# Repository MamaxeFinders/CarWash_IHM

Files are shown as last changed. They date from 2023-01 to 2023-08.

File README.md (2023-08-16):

## The whole operation is devided into the following module.

 * [**HARDWARE SETUP**](#hardware-setup)
    * [**SYSTEM MODULE**](#system-module)
    * [**CAISSE MODULE**](#caisse-module)

 * [**SOFTWARE SETUP**](#software-setup)
    * [**SYSTEM MODULE**](#module-system)
    * [**CAISSE MODULE**](#module-caisse)
    
 * [**INITIALISATION**](#initialisation)
    * [**SYSTEM INITIALISATION**](#system-initialisation)
    * [**CAISSE INITIALISATION**](#caisse-initialisation)
 
# HARDWARE SETUP

## SYSTEM MODULE

The system module utilizes the following components:
1.  [ESP32 board](https://www.espressif.com/en/products/socs/esp32)
2.  [MAX6675 thermocouple module](https://www.analog.com/media/en/technical-documentation/data-sheets/MAX6675.pdf)
3.  Four 5V LEDs is connected with the ESP32. The number of LEDs may vary depending on the number of CAISSE module.

**ESP32 board** pinout diagram:
ESP32 pinout


**MAX6675** thermocouple module pinout:
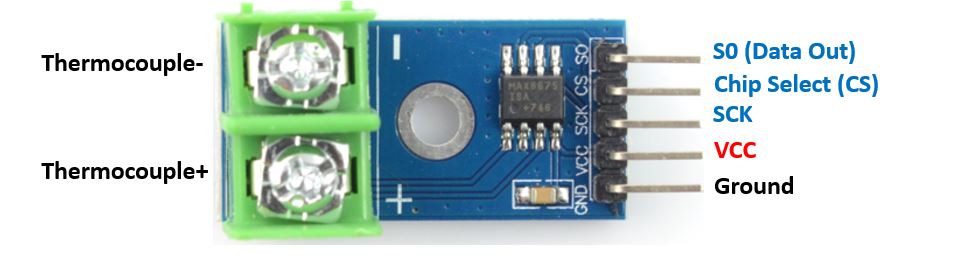
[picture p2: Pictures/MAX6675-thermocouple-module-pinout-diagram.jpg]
MAX6675 thermocouple module


The MAX6675 thermocouple is connecteded to the ESP32 as follorwing:
1.  S0 pin to GPIO27
2.  CS pin to GPIO14
3.  SCK pin to GPIO12

The four LEDs indicating CAISSE module with be connected with GPIO 19, 18 ,5, 17 of the ESP32

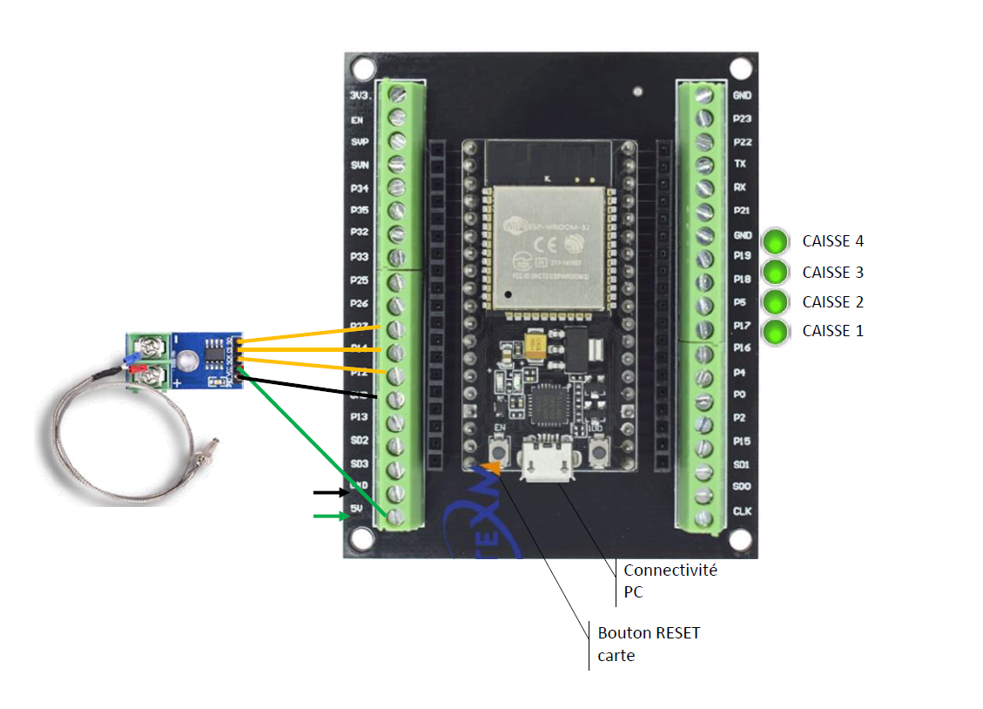
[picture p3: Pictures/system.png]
MAX6675 thermocoupleto ESP32


## CAISSE MODULE

The caisse module utilizes the following components: 
1.  [ESP32 board](https://www.espressif.com/en/products/socs/esp32)
2.  [SW-420 vibration-sensor-module](https://components101.com/sensors/sw-420-vibration-sensor-module)
3.  [2x16 LCD I2C display](https://components101.com/sites/default/files/components/16x2-LCD-Module.jpg)
4.  [8 channel 5V relay module](https://m.media-amazon.com/images/I/51BrNgOyHdL.jpg)
5.  A custom made PCB board (See GERBERS file)

**SW-420** vibration sensor module pinout diagram:
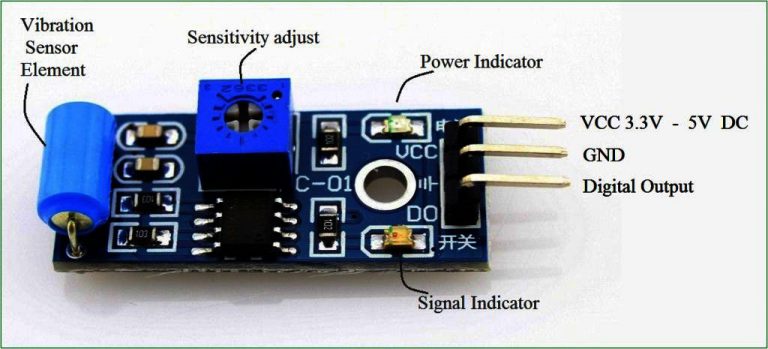
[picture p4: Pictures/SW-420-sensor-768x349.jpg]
SW-420 vibration-sensor-module pinout


**2x16 LCD I2C display** module pinout:
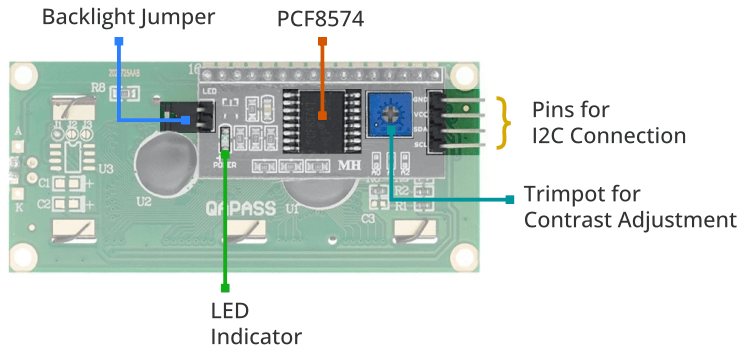
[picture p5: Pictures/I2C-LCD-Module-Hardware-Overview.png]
2x16 LCD I2C display pinout


**8 channel 5V relay** module pinout:
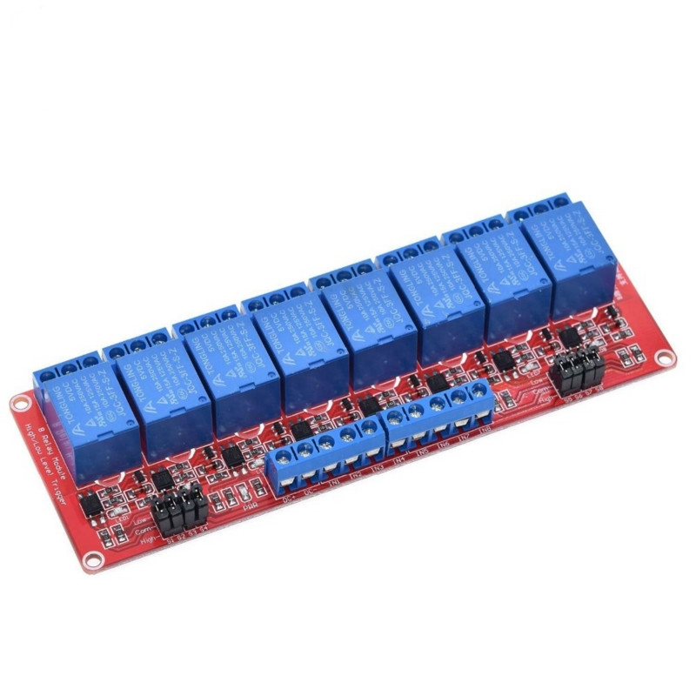
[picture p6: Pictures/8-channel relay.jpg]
8 channel 5V relay pinout


The SW-420 vibration-sensor-module is connecteded to the ESP32 as follorwing:
1.  D0 pin to GPIO13

The 2x16 LCD I2C display module is connecteded to the ESP32 as follorwing:
1.  SCL pin to GPIO22
2.  SDA pin to GPIO21

The 8 channel 5V relay module is connecteded to the ESP32 as follorwing:
1.  Relay 1 input pin to GPIO19
2.  Relay 2 input pin to GPIO18
3.  Relay 3 input pin to GPIO5
4.  Relay 4 input pin to GPIO17
5.  Relay 5 input pin to GPIO16
6.  Relay 6 input pin to GPIO4
7.  Relay 7 input pin to GPIO0
8.  Relay 8 input pin to GPIO15

### CAISSE module pcb wiring layout

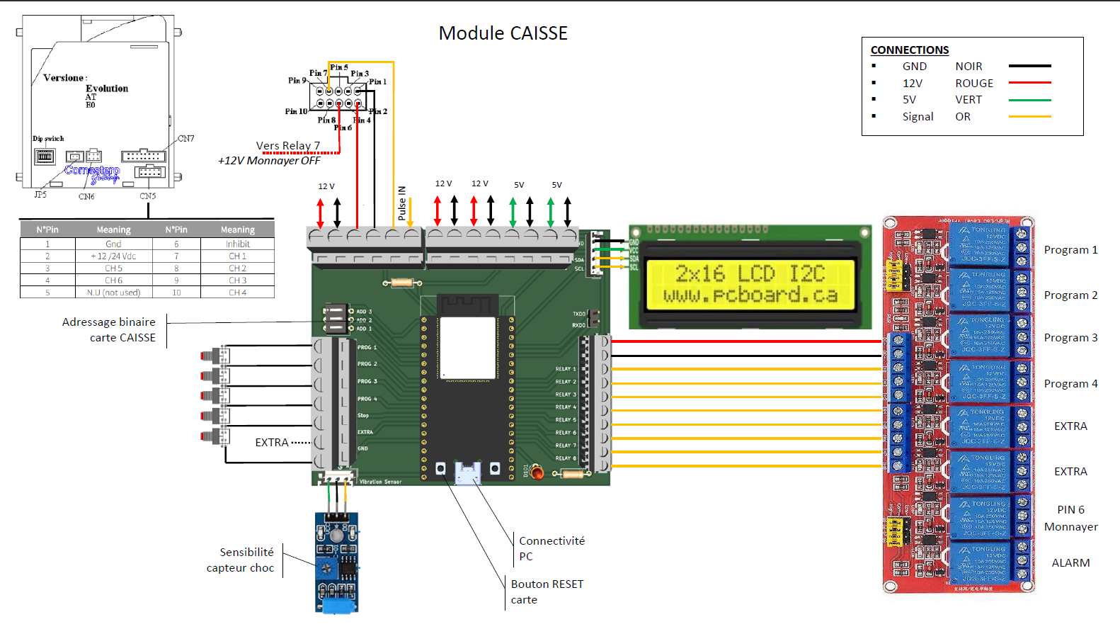
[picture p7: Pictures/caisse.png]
CAISSE module pcb wiring

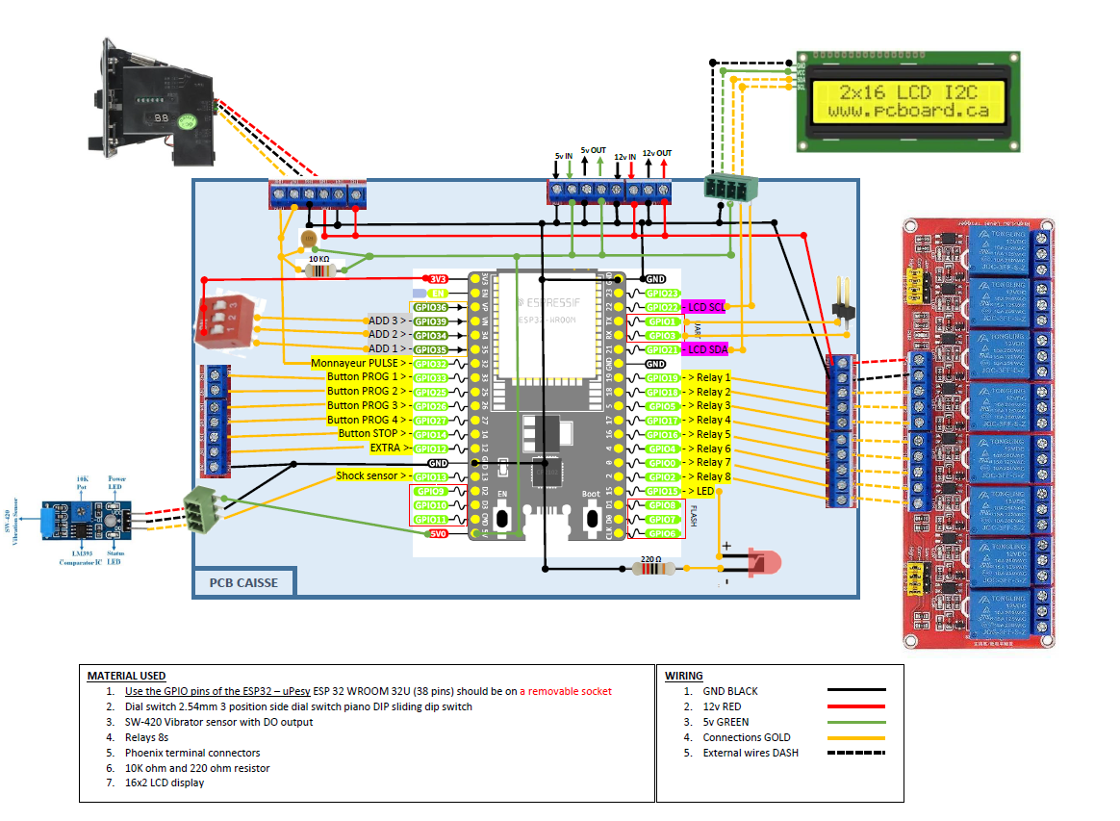
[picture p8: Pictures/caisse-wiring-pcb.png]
CAISSE module pcb schematics


### GERBER FILE
You can find the [caisse-module-gerber](https://github.com/MamaxeFinders/CarWash_IHM/tree/main/printed%20circuit%20boards) files here
 
# SOFTWARE SETUP

### ARDUINO IDE
Download and install the arduino ide by following this link [ARDUINO IDE](https://docs.arduino.cc/software/ide-v2/tutorials/getting-started/ide-v2-downloading-and-installing)

### ESP32 Add-on
Install ESP32 board add-on in Arduino IDE by following this link [ESP32 ADD-ON](https://randomnerdtutorials.com/installing-the-esp32-board-in-arduino-ide-windows-instructions/)

## Module SYSTEM

### WIFI manager library
The [*WiFiManager*](https://github.com/tzapu/WiFiManager) library for ESP32 provides an easy way to configure and manage WiFi connections in your projects. It offers features such as:
* Captive portal for setting WiFi credentials
* Ability to store WiFi credentials in Non-Volatile Memory (NVM)
* Option to automatically connect to a previously saved network
* Option to have multiple access points with custom settings
* Support for custom parameters in the configuration portal
To use the library, you can follow [this tutorial](https://microdigisoft.com/esp32-with-wifimanager-to-manage-ssid-and-password-no-hard-coding/) to setup and use the wifi-manager library. Then, you can initialize the WiFiManager object and use its functions to set up and control the WiFi connection.

### HTTPClient library
Install following this link [HTTPClient](https://github.com/amcewen/HttpClient)

### Thermocouple library
Install [MAX6675 library](https://github.com/adafruit/MAX6675-library) from the arduino library manager

### Universal Telegram Bot library
Install telegram bot library in Arduino IDE by following this link [UniversalTelegramBot](https://github.com/witnessmenow/Universal-Arduino-Telegram-Bot)

### Setup wifi as soft access point
Input your: ssid, password, channel, hide_SSID=true/false, max_connection

``` WiFi.softAP("SYSTEM_CAISSE", "123456789", CHANNEL, false, NUMSLAVES); ```

### Setup the google-script-id

``` String GOOGLE_SCRIPT_ID = "input your google-script-id here" ; ```

### Initialize Telegram BOT

``` String BOTtoken = "input your telegram bot-token here"; ```

### Compile and upload the code
Finally you can compile and upload the [system-module code](https://github.com/MamaxeFinders/CarWash_IHM/blob/main/codes/System_Auto_V3.ino) to your system module

## Module CAISSE

### LiquidCrystal_I2C library
Install [LiquidCrystal_I2C library](https://github.com/fdebrabander/Arduino-LiquidCrystal-I2C-library) from the arduino library manager

### Compile and upload the code
Finally you can compile and upload the [caisse-module code](https://github.com/MamaxeFinders/CarWash_IHM/blob/main/codes/Caisse_Auto_V3.ino) to your system module

# INITIALISATION

## SYSTEM INITIALISATION

* Turn on module SYSTEM by powering it to 5V DC. 
   * **Warning:** *Providing more than 5V will damage the module*
* Use your mobile device in order to connect to the ESP32 WiFi. Select SYSTEM_LAVAGE and connect using the password (123456789 by default).
* Wait for a windows to pop up. It will display the available networks found by the module. Click to the router you wish the module needs to connect to internet. Enter the password and click SAVE.
* Wait until the page disappear. If you go back to your WiFi settings you should now see an available SSID called SYSTEM_CAISSE which confirm the module is properly set *(DO NOT CONNECT TO THIS NEW NETWORK)*.

## CAISSE INITIALISATION

* Once the SYSTEM is connected, you can initiate the module CAISSE.
* As there can be multiple CAISSE, use the micro switch in order to address the module from 1 to 7 using the binary switches (we only used p to 4 CAISSEs here). 
* Then power it up and wait for the LED to turn on. If the module did not manage to connect to SYSTEM, the LED will blink 3 time before it restarts.
* An isolate mode is available if all switches are put to zero. The module CAISSE will start without connecting to the SYSTEM and can be used for test purpose.
* Once the module is connected and you can see the message *BONJOUR* on the LCD screen, turn OFF the module SYSTEM and ON again. Wait until the LED linked to the CAISSE id turns ON. This means both modules are ready to communicate as their mac addresses have been saved to both memories.
* Perform the same process as 2 for all other module CAISSE.

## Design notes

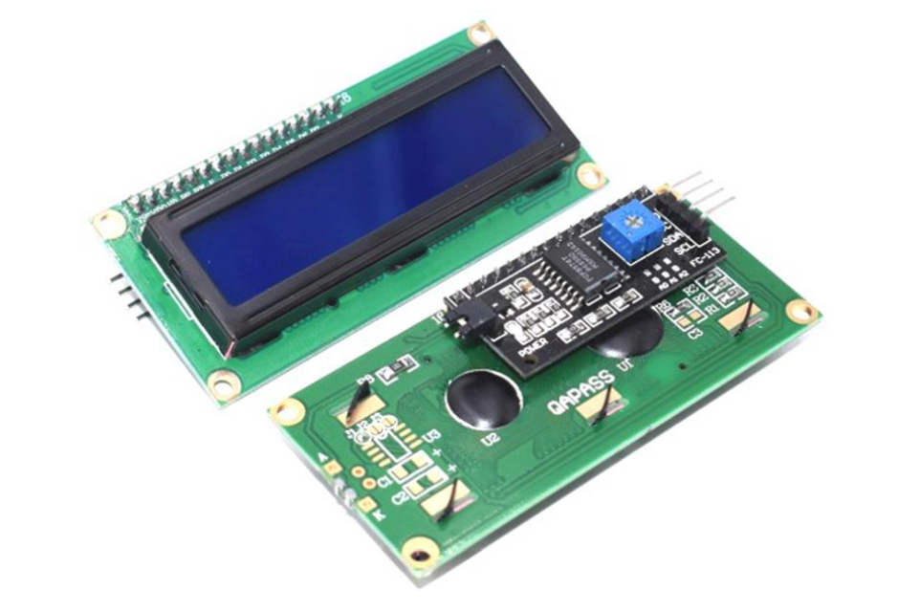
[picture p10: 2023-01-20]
Pictures/I2C-LCD-Module-Hardware-Overview2.png

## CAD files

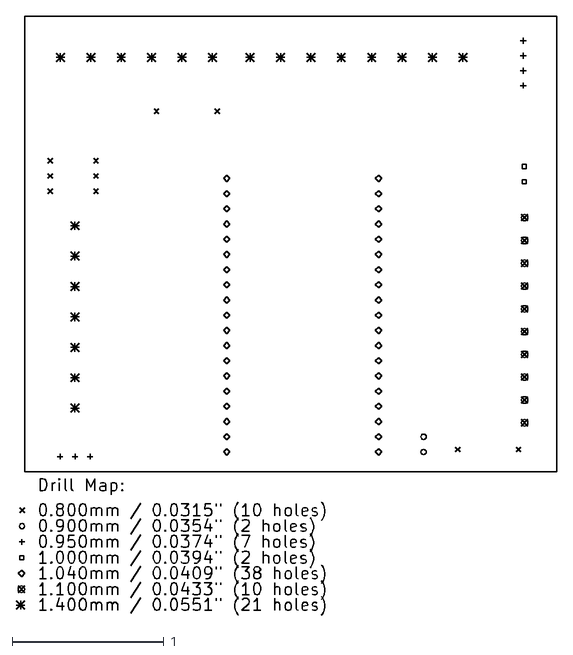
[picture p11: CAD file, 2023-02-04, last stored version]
printed circuit boards/max-PTH-drl_map.dxf
3.56 x 3.94

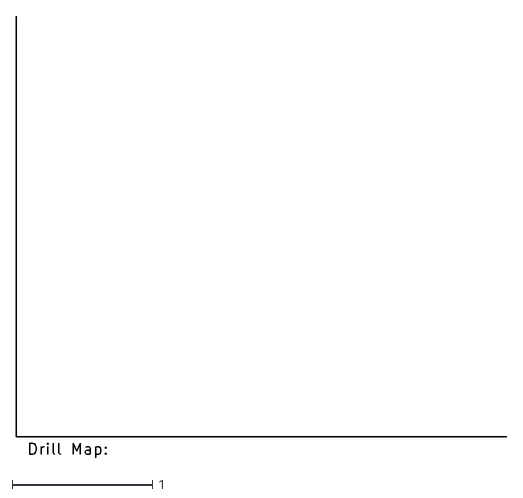
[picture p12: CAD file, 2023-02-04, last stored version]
printed circuit boards/max-NPTH-drl_map.dxf
3.50 x 3.15

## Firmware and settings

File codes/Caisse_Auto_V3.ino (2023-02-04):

#include <esp_now.h>
#include <WiFi.h>
#include <Wire.h>
#include <LiquidCrystal_I2C.h>

#define NUMSYSTEM 1
#define PRINTSCANRESULTS 0
int SystemCnt; //Count the number of SYSTEM found (should be 1 only)
int CHANNEL;
uint8_t peer_addr[6];
float Pulse_to_Credit = 1.00; //Factor for each pulse
int Initial_Credit = 0; //Initial credit entered before START
float Remaining_Credit = 0.00; //Credit left after START
long startMillis = 0;
bool Session_Started = false;
bool Button_pressed = false;
long counter = 0;
float Program_Factor[] = {0.00, 1.00, 1.00,1.00,1.00}; //Factor for each progam (Program_Factor[0] not used)

#define PULSE_INPUT 32
#define SHOCK_INPUT 13

#define PROG_1_INPUT 33
#define PROG_2_INPUT 25
#define PROG_3_INPUT 26
#define PROG_4_INPUT 27
#define STOP_INPUT 14
//#define EXTRA_INPUT 12

#define CARDADDRESS_1_IN 35
#define CARDADDRESS_2_IN 34
#define CARDADDRESS_3_IN 39
int Card_Address;

#define LED_OUT 15

#define RELAY_1_OUT 19
#define RELAY_2_OUT 18
#define RELAY_3_OUT 5
#define RELAY_4_OUT 17
#define RELAY_5_OUT 16
#define RELAY_6_OUT 4
#define RELAY_7_OUT 0
#define RELAY_8_OUT 2
int RELAYS[] = {RELAY_1_OUT,RELAY_2_OUT,RELAY_3_OUT,RELAY_4_OUT,RELAY_5_OUT,RELAY_6_OUT,RELAY_7_OUT,RELAY_8_OUT};

// ---- COOIN PULSE ---- //
unsigned long Pulse_time = 0; //variables to keep track of the timing of recent interrupts
unsigned long last_Pulse_time = 0;
volatile int Coin_Pulses = 0;
void IRAM_ATTR PULSE_PROG() {
  Pulse_time = millis();
  if (Pulse_time - last_Pulse_time > 1000) {
    last_Pulse_time = Pulse_time;
    Coin_Pulses++;
  }
}
// ---- EXTRA PULSE ---- //
unsigned long Extra_time = 0; //variables to keep track of the timing of recent interrupts
unsigned long Last_Extra_time = 0;
void IRAM_ATTR EXTRA_PROG() {
  Extra_time = millis();
  if (Extra_time - Last_Extra_time > 1000) {
    Last_Extra_time = Extra_time;
    Coin_Pulses = Coin_Pulses + 2;
  }
}

int Number_of_Shocks = 0;
bool Shock_Triggered = false;
unsigned long Shock_time = 0; //variables to keep track of the timing of recent interrupts
unsigned long last_Shock_time = 0;
volatile int Shock_count = 0;
void IRAM_ATTR SHOCK_TRIGGER(){
  if (millis() - last_Shock_time > 1000) { //Check how many pulse within 1000 ms
    last_Shock_time = Shock_time;
    if(Shock_count > 80){Shock_Triggered = true;}
  }  Shock_count++;
}

// ---- BUTTONS WITH INTERRUPT ---- //
volatile int BUTTON_PROG = 0;
void IRAM_ATTR BUTTON_PROG_1() {BUTTON_PROG = 1;}
void IRAM_ATTR BUTTON_PROG_2() {BUTTON_PROG = 2;}
void IRAM_ATTR BUTTON_PROG_3() {BUTTON_PROG = 3;}
void IRAM_ATTR BUTTON_PROG_4() {BUTTON_PROG = 4;}
void IRAM_ATTR BUTTON_STOP() {BUTTON_PROG = 10;}

LiquidCrystal_I2C lcd(0x27, 16, 2); // set the LCD address to 0x27 for a 16 chars and 2 line display

esp_now_peer_info_t System[NUMSYSTEM] = {};
typedef struct struct_System_Info  {/*KEEP*/
  int System_Number;
  String System_SSID;
  String System_MAC;
  int32_t System_Signal;
  int8_t System_isFauly;
} struct_System_Info; struct_System_Info System_Info; /*KEEP*/

typedef struct struct_message_to_System { /*KEEP*/
  int CardCAISSE;
  int Request = 0;
  float Credit = 00.00;
  int RequestCode = 0;
  int Shocks = 0;
} struct_message_to_System; struct_message_to_System message_to_System; /*KEEP*/

typedef struct struct_message_From_System { /*KEEP*/
  int CardCAISSE;
  int Request;
  float Credit;
  int Message;
} struct_message_From_System; struct_message_From_System message_From_System; /*KEEP*/

// ---- SEND DATA ---- //
esp_now_peer_info_t peerInfo; /*KEEP*/
void OnDataSent(const uint8_t *mac_addr, esp_now_send_status_t status) { /*KEEP*/
  char macStr[18];
  int MACtest = snprintf(macStr, sizeof(macStr), "%02x:%02x:%02x:%02x:%02x:%02x", mac_addr[0], mac_addr[1], mac_addr[2], mac_addr[3], mac_addr[4], mac_addr[5]);
  Serial.print("Last Packet Sent to: "); Serial.println(MACtest); //Serial.println(macStr);
  Serial.println(status == ESP_NOW_SEND_SUCCESS ? "Delivery Success" : "Delivery Fail");
}
void SendMessage(int a, int b, float c, int d, int e) { // send data
  if(Card_Address > 0){
  message_to_System.CardCAISSE = a;
  message_to_System.Request = b;
  message_to_System.Credit = c;
  message_to_System.RequestCode = d;
  message_to_System.Shocks = e;

  char macStr[18];snprintf(macStr, sizeof(macStr), "%02x:%02x:%02x:%02x:%02x:%02x",peer_addr[0], peer_addr[1], peer_addr[2], peer_addr[3], peer_addr[4], peer_addr[5]);
  memcpy(&peerInfo.peer_addr, peer_addr, 6);
  Serial.print("Peer MAC2: "); Serial.println(macStr);
  if (!esp_now_is_peer_exist(peer_addr)) {esp_now_add_peer(&peerInfo);}
  esp_err_t result = esp_now_send(peer_addr, (uint8_t *) &message_to_System, sizeof(message_to_System));
  if (result == ESP_OK)  {Serial.println("Message sent");}
  else if (result == ESP_ERR_ESPNOW_NOT_INIT)  {Serial.println("ESPNOW not Init.");}
  else if (result == ESP_ERR_ESPNOW_ARG)       {Serial.println("Invalid Argument");}
  else if (result == ESP_ERR_ESPNOW_INTERNAL)  {Serial.println("Internal Error");}
  else if (result == ESP_ERR_ESPNOW_NO_MEM)    {Serial.println("ESP_ERR_ESPNOW_NO_MEM");}
  else if (result == ESP_ERR_ESPNOW_NOT_FOUND) {Serial.println("Peer not found.");}
  else  {Serial.println("Unknown error");}
  }}

// ---- callback when data is recv from System ---- //
void OnDataRecv(const uint8_t *mac_addr, const uint8_t *incomingData, int data_len) {
  char macStr[18];
  snprintf(macStr, sizeof(macStr), "%02x:%02x:%02x:%02x:%02x:%02x",mac_addr[0], mac_addr[1], mac_addr[2], mac_addr[3], mac_addr[4], mac_addr[5]);
  memcpy(&message_From_System, incomingData, sizeof(message_From_System));
  Serial.print("Massage received by: "); Serial.println(macStr);
  Serial.print("Data size: "); Serial.println(sizeof(message_From_System));
    if(message_From_System.Request == 2){ // Request 2 for Credit
      Serial.print("New Credit of: "); Serial.println(message_From_System.Credit);
      Coin_Pulses = Coin_Pulses + message_From_System.Credit;
    }
}
// ======================================== SETUP ======================================== //
void setup() {
  Serial.begin(115200);
  // ---- PINS SETUP ---- //
  pinMode(LED_OUT, OUTPUT);
  pinMode(RELAY_1_OUT, OUTPUT); pinMode(RELAY_2_OUT, OUTPUT); pinMode(RELAY_3_OUT, OUTPUT); pinMode(RELAY_4_OUT, OUTPUT);
  pinMode(RELAY_6_OUT, OUTPUT); pinMode(RELAY_7_OUT, OUTPUT); pinMode(RELAY_4_OUT, OUTPUT); pinMode(RELAY_8_OUT, OUTPUT);
  pinMode(SHOCK_INPUT, INPUT_PULLUP);attachInterrupt(digitalPinToInterrupt(SHOCK_INPUT), SHOCK_TRIGGER, RISING);
  pinMode(PULSE_INPUT, INPUT_PULLUP);attachInterrupt(digitalPinToInterrupt(PULSE_INPUT), PULSE_PROG, FALLING);
  pinMode(PROG_1_INPUT, INPUT_PULLUP);attachInterrupt(digitalPinToInterrupt(PROG_1_INPUT), BUTTON_PROG_1, FALLING);
  pinMode(PROG_2_INPUT, INPUT_PULLUP);attachInterrupt(digitalPinToInterrupt(PROG_2_INPUT), BUTTON_PROG_2, FALLING);
  pinMode(PROG_3_INPUT, INPUT_PULLUP);attachInterrupt(digitalPinToInterrupt(PROG_3_INPUT), BUTTON_PROG_3, FALLING);
  pinMode(PROG_4_INPUT, INPUT_PULLUP);attachInterrupt(digitalPinToInterrupt(PROG_4_INPUT), BUTTON_PROG_4, FALLING);
  pinMode(STOP_INPUT, INPUT_PULLUP);attachInterrupt(digitalPinToInterrupt(STOP_INPUT), BUTTON_STOP, FALLING);

  // -- CARD ADDRESS -- //
  pinMode(CARDADDRESS_1_IN, INPUT); /*KEEP*/
  pinMode(CARDADDRESS_2_IN, INPUT); /*KEEP*/
  pinMode(CARDADDRESS_3_IN, INPUT); /*KEEP*/
  delay(2000);
  Card_Address = digitalRead(CARDADDRESS_1_IN) * 1 + digitalRead(CARDADDRESS_2_IN) * 2 + digitalRead(CARDADDRESS_3_IN) * 4;
  System_Info.System_SSID = "CAISSE" + String(Card_Address);
  Serial.print("CardCAISSE_ID : ");Serial.println(System_Info.System_SSID);

  // ---- LCD SETUP ----//
  lcd.init();  // initialize the lcd
  lcd.backlight();
  lcd.clear();
  lcd.setCursor(0, 0); lcd.print(" INITIALISATION ");
  lcd.setCursor(0, 1); lcd.print(String(System_Info.System_SSID));

  // ---- WIFI SETUP ----//
  if(Card_Address == 0){
    Serial.println("MODE SOLO");
    Coin_Pulses = 2.00;
    for(int i=0;i<2;i++){
      digitalWrite(LED_OUT, HIGH);delay(1000);
      digitalWrite(LED_OUT, LOW);delay(1000);
    }
  }else{
    ScanForSystem();
    configDeviceAP(System_Info.System_SSID);
    InitESPNow();    
    Serial.print("CAISSE OK : ");Serial.print("AP MAC: "); Serial.println(WiFi.softAPmacAddress());
  }
 
  Set_Relays(7); //Acctivate coin acceptor
  digitalWrite(LED_OUT, HIGH);
  lcd.clear();    
  lcd.setCursor(0, 0); lcd.print("BONJOUR         ");
  lcd.setCursor(0, 1); lcd.print("INSEREZ PIECE   ");
}
// ======================================== LOOP ======================================== //
void loop() {
// ---- IF SHOCK ---- //
  if(Shock_Triggered){
    Shock_Triggered = false;
    Number_of_Shocks++;
    Serial.print("NUMBER OF SHOCKS : ");Serial.println(Number_of_Shocks);   
    for(int s = 0; s < Number_of_Shocks; s++){
      lcd.clear();lcd.setCursor(0, 1); lcd.print("! ALERTE CHOC !");
      Set_Relays(8); // Alarm
      delay(1000);
      if(Number_of_Shocks > 2){ //Stop the program at third shock
        delay(5000);
        BUTTON_PROG = 10;
        Number_of_Shocks = 0;
      }
      Set_Relays(0);
      delay(1000);
    }
    if(Coin_Pulses == 0 && BUTTON_PROG < 1){
      lcd.clear();    
      lcd.setCursor(0, 0); lcd.print("BONJOUR         ");
      lcd.setCursor(0, 1); lcd.print("INSEREZ PIECE   ");
    }
    SendMessage(Card_Address, 9, Remaining_Credit,BUTTON_PROG,Number_of_Shocks); //Send CardCAISSE,Request,Credit,RequestCode
  } else if (BUTTON_PROG == 10 || Remaining_Credit < 0) {
// PROGRAM STOP //
    Serial.println("COUNT STOP");
    lcd.clear();lcd.setCursor(6, 1);lcd.print("STOP");
    Initial_Credit = 0; //Initial credit entered before START
    Remaining_Credit = 0; //Credit left after START
    startMillis = 0;
    Session_Started = false;
    Button_pressed = false;
    counter = 0;
    Coin_Pulses = 0;
    BUTTON_PROG = 0;
    Number_of_Shocks = 0;
    Set_Relays(0);
    delay(5000);
    lcd.clear();
    lcd.setCursor(0, 0); lcd.print("BONJOUR         ");
    lcd.setCursor(0, 1); lcd.print("INSEREZ PIECE   ");
    Set_Relays(7); //Activate coin acceptor
  }else if (Coin_Pulses > 0 && BUTTON_PROG < 1) {
// ---- IF FIRST COIN INSERTED ---- //    
    Number_of_Shocks = 0;
    Initial_Credit = Pulse_to_Credit * Coin_Pulses;
    Remaining_Credit = Initial_Credit;
    Serial.print("INITIAL CREDIT : ");
    Serial.println(Initial_Credit);
    lcd.clear();
    lcd.setCursor(0, 1);
    lcd.print("CREDIT : " + String(float(Initial_Credit)) + " E");  
  } else if (BUTTON_PROG > 0 && Initial_Credit > 0) {
// ---- PROGRAM START ---- //      
    if (!Session_Started) {
      startMillis = millis();
      Coin_Pulses = 0;
      Session_Started = true;
      Remaining_Credit = Initial_Credit;
      SendMessage(Card_Address, 1, Remaining_Credit, BUTTON_PROG,0); //Send CardCAISSE,Request,Credit,RequestCode
    }
    Set_Relays(BUTTON_PROG);
    counter = (millis() - startMillis) / 1000;
    startMillis = millis();
    Remaining_Credit = Remaining_Credit - ((float)counter * Program_Factor[BUTTON_PROG] / 20.0 / 3.0); // equivalent to 5 sents every 1 sec
    Serial.print("PROGRAM : "); Serial.print(String(BUTTON_PROG));Serial.print(" REM CREDIT : "); Serial.println(String(Remaining_Credit));
    lcd.setCursor(0, 0);lcd.print("PROGRAM  " + String(BUTTON_PROG) + "      ");
    lcd.setCursor(0, 1);lcd.print("CREDIT : " + String(float(Remaining_Credit)) + " E");
  }
  delay(1000);
}
// ======================================== FUNCTIONS ======================================== //
// ---- SET RELAYS ---- //
void Set_Relays(int v){
  for(int p = 1; p <= (sizeof(RELAYS)/sizeof(RELAYS[0])) ; p++){
    if(v == p){
      digitalWrite(RELAYS[p-1], HIGH);
    }else{
      digitalWrite(RELAYS[p-1], LOW);
    }
  }
}

// ---- Init ESP Now with fallback ---- //
void InitESPNow() {
  WiFi.disconnect();
  if (esp_now_init() == ESP_OK) {
    Serial.println("ESPNow Init Success");
    esp_now_register_send_cb(OnDataSent);
    esp_now_register_recv_cb(OnDataRecv);
  }  else {
    Serial.println("ESPNow Init Failed");
    ESP.restart();
  }
}

// ---- config AP SSID ---- //
void configDeviceAP(String SSID) {
  String Password = "123456789";
  bool result = WiFi.softAP(SSID.c_str(), Password.c_str(), CHANNEL, 0);
  if (!result) {
    Serial.println("AP Config failed.");
  } else {
    Serial.print("AP Config Success for : ");
    Serial.println(String(SSID));
  }
}

// ---- SCAN FOR SYSTEM ----//
void ScanForSystem() {
  WiFi.mode(WIFI_AP_STA); //Optional
  int8_t scanResults = WiFi.scanNetworks();
  memset(System, 0, sizeof(System));
  SystemCnt = 0;
  if (scanResults == 0) {
    Serial.println("No WiFi devices in AP Mode found");
  } else {
    Serial.print("Found "); Serial.print(scanResults); Serial.println(" devices ");
    for (int i = 0; i < scanResults; ++i) {
      // Print SSID and RSSI for each device found
      String SSID = WiFi.SSID(i); //Provide the name of the network found
      int32_t RSSI = WiFi.RSSI(i); //Check signal performances from -100 to 0
      String BSSIDstr = WiFi.BSSIDstr(i); //Basic Service Set Identification) that is another name of MAC address of a network discovered during the scan
      if (PRINTSCANRESULTS) {
        Serial.print(i + 1); Serial.print(": "); Serial.print(SSID); Serial.print(" ["); Serial.print(BSSIDstr); Serial.print("]"); Serial.print(" ("); Serial.print(RSSI); Serial.print(") ch: "); Serial.println(CHANNEL);
      }
      delay(10);
      // Check if the current device starts with `CAISSE`
      if (SSID.indexOf("SYSTEM_CAISSE") == 0 && SystemCnt < NUMSYSTEM) {
        CHANNEL = WiFi.channel(i);
        Serial.print(i + 1); Serial.print(": "); Serial.print(SSID); Serial.print(" ["); Serial.print(BSSIDstr); Serial.print("]"); Serial.print(" ("); Serial.print(RSSI); Serial.print(") ch: "); Serial.println(CHANNEL);
        // Get BSSID => Mac Address of the System
        int mac[6];
        if ( 6 == sscanf(BSSIDstr.c_str(), "%x:%x:%x:%x:%x:%x",  &mac[0], &mac[1], &mac[2], &mac[3], &mac[4], &mac[5]) ) {
          for (int ii = 0; ii < 6; ++ii ) {
            System[SystemCnt].peer_addr[ii] = (uint8_t) mac[ii];
            peer_addr[ii] = (uint8_t) mac[ii]; // For unique SYSTEM
          }
        }
        System[SystemCnt].channel = CHANNEL; // pick a channel
        System[SystemCnt].encrypt = 0; // no encryption
        esp_err_t addStatus = esp_now_add_peer(&System[SystemCnt]);
        if (addStatus == ESP_OK) {// Pair success
          Serial.println("Pair success");
          System_Info.System_Number = SystemCnt + 1;
          System_Info.System_SSID = SSID;
          System_Info.System_MAC = BSSIDstr;
          System_Info.System_Signal = RSSI;
          System_Info.System_isFauly = 0;
        } else if (addStatus == ESP_ERR_ESPNOW_NOT_INIT) {Serial.println("ESPNOW Not Init");
        } else if (addStatus == ESP_ERR_ESPNOW_ARG) {Serial.println("Add Peer - Invalid Argument");
        } else if (addStatus == ESP_ERR_ESPNOW_FULL) {Serial.println("Peer list full");
        } else if (addStatus == ESP_ERR_ESPNOW_NO_MEM) {Serial.println("Out of memory");
        } else if (addStatus == ESP_ERR_ESPNOW_EXIST) {Serial.println("Peer Exists");
        } else {Serial.println("Not sure what happened");}
        SystemCnt++;
      }
    }
  }
  if (SystemCnt > 0) {Serial.print(SystemCnt); Serial.println(" SYSTEM found,");
  } else {Serial.print("No SYSTEM Found => Restarting");
    for(int i = 0; i < 3; i++){
      Serial.print(".");
      digitalWrite(LED_OUT, HIGH);delay(200);
      digitalWrite(LED_OUT, LOW);delay(200);
    }Serial.println(".");
    lcd.clear();
    delay(2000);
    ESP.restart();
  }
  WiFi.scanDelete();// clean up ram
}

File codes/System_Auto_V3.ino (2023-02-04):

#include <esp_now.h>
#include <WiFi.h>
#include <WiFiManager.h> // https://github.com/tzapu/WiFiManager //https://microdigisoft.com/esp32-with-wifimanager-to-manage-ssid-and-password-no-hard-coding/
#include <HTTPClient.h>

// -- TEMP SENSOR -- //
#include "max6675.h"
#define RELAY_OUT 26
int thermoCLK = 12;
int thermoCS = 14;
int thermoDO = 27;
float Temp_Value;
float Min_Temperature = 2.00;
bool Bot_Temperature = false;
MAX6675 thermocouple(thermoCLK, thermoCS, thermoDO);

// -- TELEGRAM -- //
#include <WiFiClientSecure.h>
#include <UniversalTelegramBot.h>

#define LED_CAISSE1 17
#define LED_CAISSE2 5
#define LED_CAISSE3 18
#define LED_CAISSE4 19

// VARIABLES FOR PAIRING
#define NUMSLAVES 20
#define PRINTSCANRESULTS 0
// Google script ID and required credentials
String GOOGLE_SCRIPT_ID = "AKfycbziCv5KrLd04WmRT_k1B10jjVmOscfB7w6_DkPbByOzOITigoVcK06lYO42ExSkvbdJ";    // change Gscript ID
unsigned long Check_time = 0; //variables to keep track of the timing of recent interrupts
unsigned long last_Check_time = 0;

esp_now_peer_info_t slaves[NUMSLAVES] = {};
int CHANNEL = 1;
int SlaveCnt;
String Faulty_MAC_address;

// Initialize Telegram BOT
String BOTtoken = "XXXXXXXXXXXXXXXXXXXXX";  // your Bot Token (Get from Botfather)
String CHAT_ID; // "XXXXXXXXXXXXX"
WiFiClientSecure client;
UniversalTelegramBot bot(BOTtoken, client);

bool CAISSE_response_OK = false;
String messages = "";
String messageSHOCK = "";
String Bot_Message = "";
typedef struct struct_Slaves_Info  {/*KEEP*/
int Slave_Number[NUMSLAVES];
String Slave_SSID[NUMSLAVES]; 
uint8_t Slave_MAC[NUMSLAVES][6]; 
int32_t Slave_Signal[NUMSLAVES];
unsigned int Slave_isFauly[NUMSLAVES];
}struct_Slaves_Info; struct_Slaves_Info Slaves_Info; /*KEEP*/

typedef struct struct_message_to_Caisse { /*KEEP*/
int CardCAISSE; 
int Request = 0;
float Credit = 00.00; 
int Message = 0;} struct_message_to_Caisse;
struct_message_to_Caisse message_to_Caisse; /*KEEP*/

typedef struct struct_message_From_Caisse { /*KEEP*/
int CardCAISSE; 
int Request;
float Credit; 
int Message;
int Shocks;} struct_message_From_Caisse;
struct_message_From_Caisse message_From_Caisse; /*KEEP*/

// send data and confirm the message was sent
void SendMessage(String a, int b, float c, int d, uint8_t peer_addr[6]) {
  message_to_Caisse.Request = b;
  message_to_Caisse.Credit = c;
  message_to_Caisse.Message = d;
  char macStr[18];
  snprintf(macStr, sizeof(macStr), "%02x:%02x:%02x:%02x:%02x:%02x",peer_addr[0], peer_addr[1], peer_addr[2], peer_addr[3], peer_addr[4], peer_addr[5]);
    esp_err_t result = esp_now_send(peer_addr, (uint8_t *) &message_to_Caisse, sizeof(message_to_Caisse));
    Serial.print("Send Status for: ");Serial.print(a); Serial.print(" : ");Serial.print(macStr);Serial.print(" : ");
    if (result == ESP_OK) { Serial.println("Success");
    } else if (result == ESP_ERR_ESPNOW_NOT_INIT) {Serial.println("ESPNOW not Init.");
    } else if (result == ESP_ERR_ESPNOW_ARG) {Serial.println("Invalid Argument");
    } else if (result == ESP_ERR_ESPNOW_INTERNAL) {Serial.println("Internal Error");
    } else if (result == ESP_ERR_ESPNOW_NO_MEM) {Serial.println("ESP_ERR_ESPNOW_NO_MEM");
    } else if (result == ESP_ERR_ESPNOW_NOT_FOUND) {Serial.println("Peer not found.");
    } else {Serial.println("Not sure what happened");}
  delay(500); //Wait for callback feedback before sending another message
}
// callback when data is sent from SYSTEM to CAISSE and check receiving status
void OnDataSent(const uint8_t *mac_addr, esp_now_send_status_t status) {
  char macStr[18];
  snprintf(macStr, sizeof(macStr), "%02x:%02x:%02x:%02x:%02x:%02x",mac_addr[0], mac_addr[1], mac_addr[2], mac_addr[3], mac_addr[4], mac_addr[5]);
  Serial.print("Last Packet Sent to: "); Serial.println(macStr); //Serial.println(macStr);
  if(status == ESP_NOW_SEND_SUCCESS){Serial.println("MAC acknoledge : SUCCESS");
    CAISSE_response_OK = true;
  }else{Serial.println("MAC acknoledge : FAILED");
    CAISSE_response_OK = false; 
  }   
}

// callback when data is recv from Master
void OnDataRecv(const uint8_t *mac_addr, const uint8_t *incomingData, int data_len) {
  char macStr[18];
  snprintf(macStr, sizeof(macStr), "%02x:%02x:%02x:%02x:%02x:%02x",mac_addr[0], mac_addr[1], mac_addr[2], mac_addr[3], mac_addr[4], mac_addr[5]);
  memcpy(&message_From_Caisse, incomingData, sizeof(message_From_Caisse));
  Serial.print("Last Packet Recv from: "); Serial.print(macStr);Serial.print(" : Size: "); Serial.println(sizeof(message_From_Caisse));
  if(message_From_Caisse.Request == 1){ //PROGEM received, send data to Google
    messages = "message=PROGRAM&status=ok&caisse=" + String(message_From_Caisse.CardCAISSE) + "&credit=" + String(message_From_Caisse.Credit); 
  }else if(message_From_Caisse.Request == 9){ //Send Alert to Telegram Bot
    messages = "message=SHOCK&status=Shock&caisse=" + String(message_From_Caisse.CardCAISSE) + "&credit=" + String(message_From_Caisse.Credit);
    messageSHOCK = message_From_Caisse.CardCAISSE;
  }else{
    Serial.println("MESSAGE RECEIVED UNKNOWN !");
  }
}
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
